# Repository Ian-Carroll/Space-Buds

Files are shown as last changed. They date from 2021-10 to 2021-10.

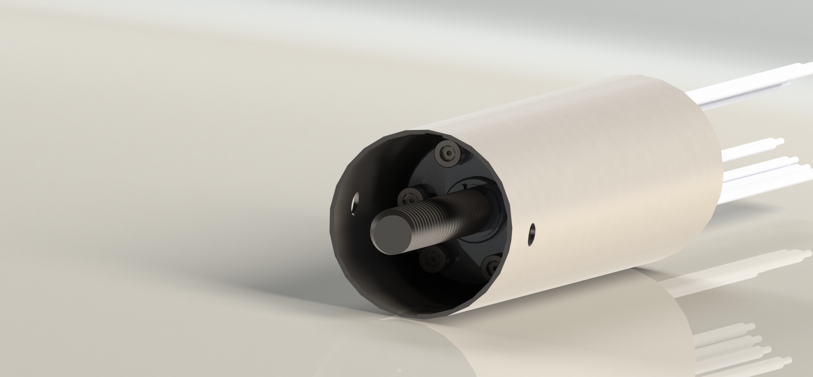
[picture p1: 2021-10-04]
Mechanical/Renders/male_side.jpeg

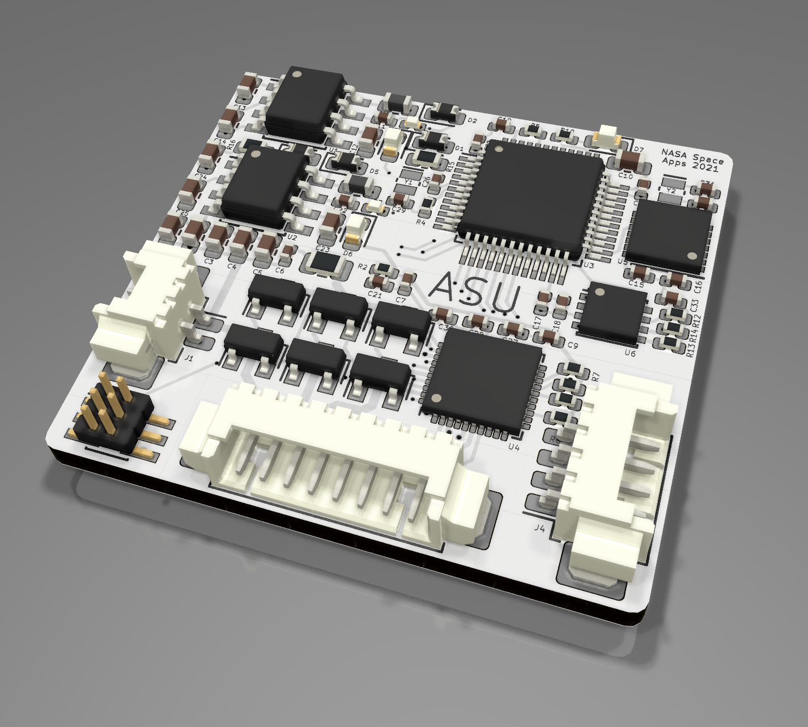
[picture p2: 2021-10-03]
Electrical/Renders/right_angle.png

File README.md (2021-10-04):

# Space Buds 

Space Buds team repository for NASA's 2021 International Space Apps Challenge - "Let It Go (Without A Bang)".

Please find our pitch video [here](https://www.youtube.com/watch?v=mZa6cD9xq2c), or feel free to browse this repository for more information. This README provides an overview of the information contained within the repository.

We would also like to highlight our design report, which can be found under `Documentation/report.pdf`.

## Mechanical Design
ezgif com-gif-maker
[Please note that the gearbox casing should not be spinning in the above animation, and the spring is missing]




[Please note that the spring should be compressed in the above render]

## Electrical Design

left_angle
right_angle
layout
schematic

## Documentation Files
File | Contents
---- | --------
`Documentation/report.pdf` | A complete design report detailing every aspect of our project. Includes renders, drawings and references.
`Documentation/presentation.pdf` | Our 5-slide pitch presentation, presented [here](https://www.youtube.com/watch?v=mZa6cD9xq2c).
`Documentation/Datasheets/Electrical/` | Datasheets for all off-the-shelf mechanical components used in our design.
`Documentation/Datasheets/Mechanical/` | Datasheets for all off-the-shelf electrical components used in our design.

## Mechanical Files
File | Contents
---- | --------
`Mechanical/animation.mp4` | An animation of the system deploying.
`Mechanical/Drawings/SolidWorks/` | SolidWorks mechanical drawings files.
`Mechanical/Drawings/Images/` | SolidWorks mechanical drawings as JPEG or PDF files.
`Mechanical/Models/SolidWorks/` | SolidWorks 3D model files.
`Mechanical/Renders/` | Mechanical part renders.

## Electrical Files

File | Contents
---- | --------
`Electrical/KiCad/` | KiCAD electrical CAD files for the PCB.
`Electrical/Renders/` | Renders of the PCB, generated by KiCAD.
`Electrical/layout.png` | An image of the PCB's layout.
`Electrical/schematic.png` | An image of the PCB's schematic.

## Contributors

* Noah Bailey
* Ian Carroll
* Aidan Clark
* Nick Cusack
* Madison Squires
* Shane Williams

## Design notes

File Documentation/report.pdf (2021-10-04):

October 2nd & 3rd, 2021 | All Screwed Up!

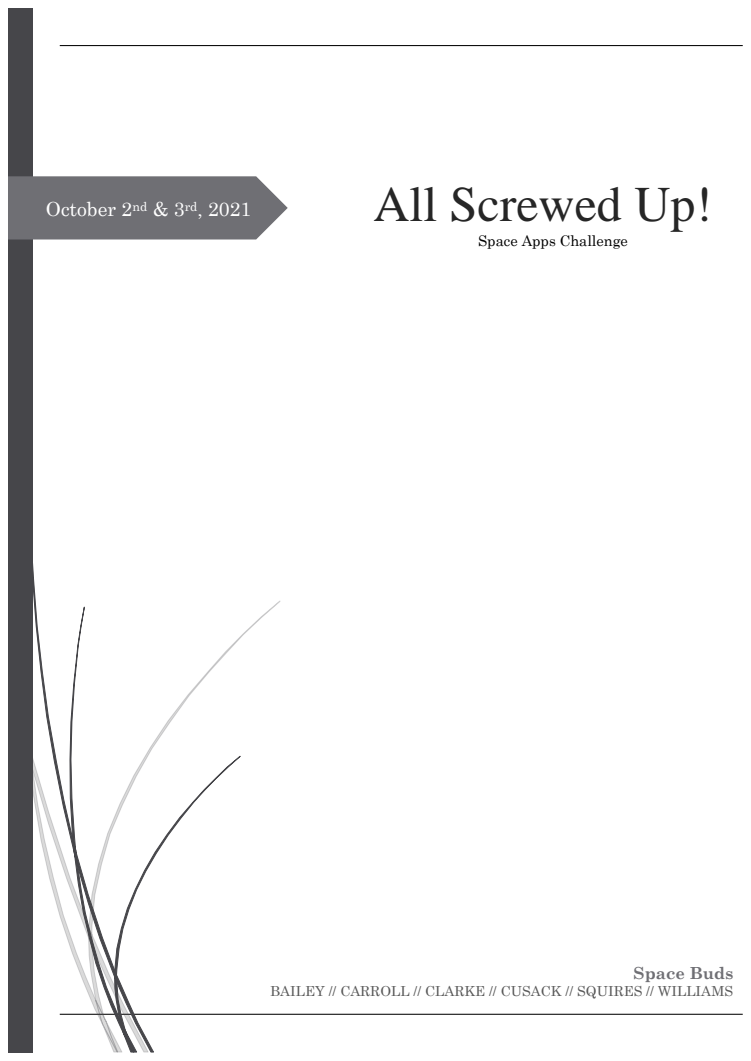
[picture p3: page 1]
Space Buds

Space Apps Challenge

BAILEY // CARROLL // CLARKE // CUSACK // SQUIRES // WILLIAMS

All Screwed Up! | Space Buds
Page | ii

## Table of Contents

Page | iii

Page | iv

## List Of Acronyms

By order of appearance

Acronym -=-=-=-=-=-=-=-=-=-=- Expansion

MUN | Memorial University of Newfoundland
ECE | Electrical Computer Engineer
CAD | Computer Automated Design
CWSF | Canada Wide Science Fair
STEM | Science, Technology, Engineering, Mathematics
NASA | National Aeronautics and Space Administration
FEA | Finite Element Analysis
3D | Three-Dimension // Three-Dimensional
PCB | Printed Circuit Board
CAN | Controller Area Network
ASU | All Screwed Up!
RPM | Revolutions Per Minute
W | Watt(s)
mm | Millimeter(s)
A // Amp | Ampere(s)
V | Volt(s)
N-m | Newton-meter(s)
N | Newton(s)
IC | Integrated Circuit

## 1 – Meet the Team

The Space Buds team is composed of six Engineering students enrolled in Memorial University

of Newfoundland. All members of the team are in their third year of the program, with an

expected graduation in 2024. The team, composed of two Mechanical Engineering students, two

Electrical Engineering students, and two Computer Engineering students – along with a wide

variety of work experience and interests – is capable of handling a large variety of challenges of

any sort.

## Noah Bailey

Coming from a family full of engineers and scientists, Noah grew up eager to study and become

an engineer just like those around him. A resident of Newfoundland his whole life, Noah is

starting his third year of Electrical Engineering at MUN. Noah developed a love for all things

computer and electrical at a young age, guiding him to inevitably study within the Electrical

Computer Engineer (ECE) program

provided at his local university.

He is interested in computing hardware,

sound engineering and music production,

physics, graphic design, and writing.

His skills include coding in various

languages, mathematics, and Computer

automated design.

Noah is competing in the Nasa SpaceApps

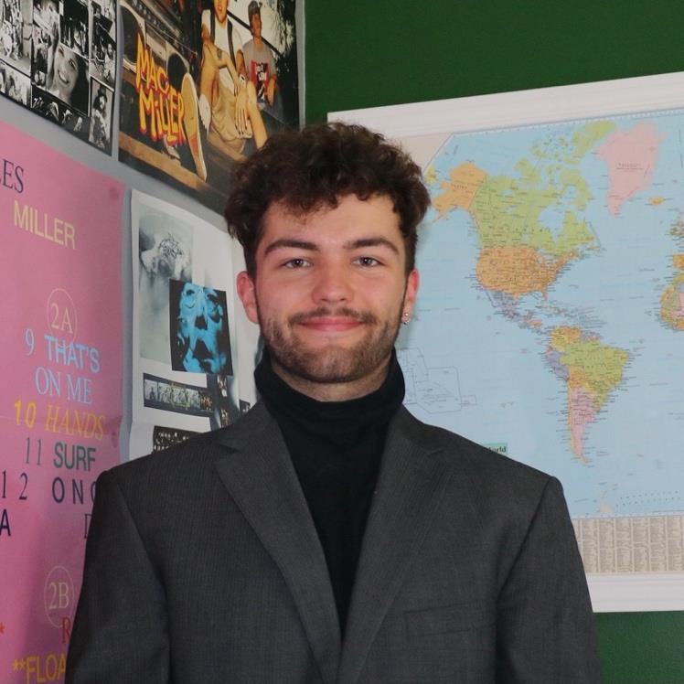
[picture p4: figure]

challenge for his first time this year and is hoping to make a big impact along with his talented

team members and classmates.

## Ian Carroll

Ian is starting his third year of Computer Engineering at Memorial University. He is always

eager to learn something new; over the last year, Ian

has learned numerous programming languages and

frameworks, taking a particular interest in

electronics and embedded system development.

Ian’s interests include choral singing, performing in

plays and musicals, and playing basketball. This

year is the first time Ian has competed in the Space

Apps international hackathon. However, he is very

excited to learn new things about hardware

development and apply them to real-world problems.

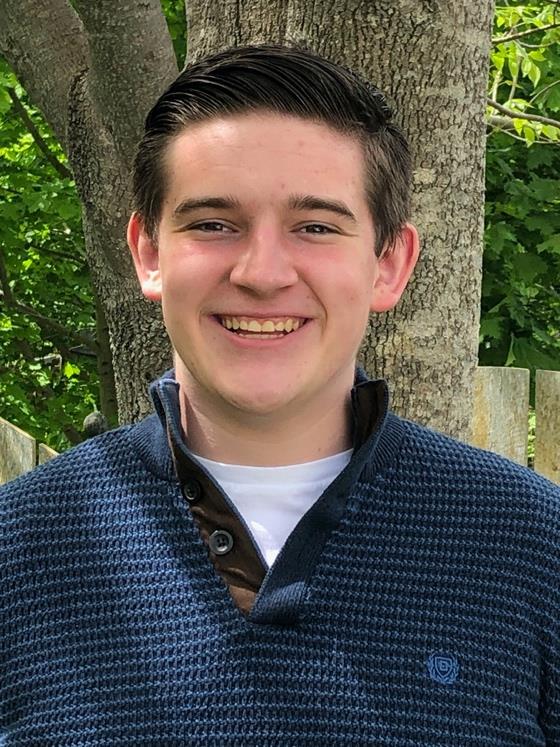
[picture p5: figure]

Ian's already existing skills include C/C++ development for embedded systems, C#

programming for cross-platform applications, and various applications of CAD development.

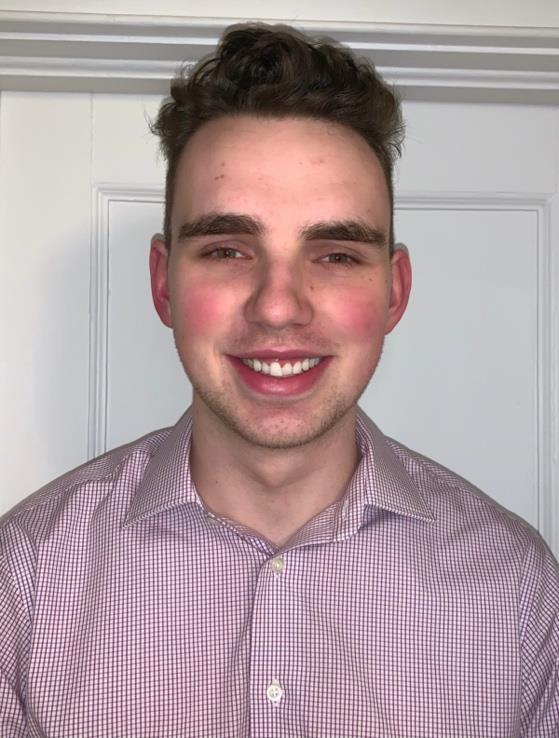
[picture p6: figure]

## Aidan Clark

Aidan Clark is a third-year Mechanical Engineering

student from a small town in Nova Scotia, currently

studying at Memorial University of Newfoundland.

Growing up, Aidan always had an interest in

learning more about how things worked - which is

why he decided to pursue a degree in engineering.

In his free time, he enjoys spending time outdoors,

exploring the rugged Newfoundland coast, or playing

volleyball.

This is Aidan’s first Space Apps competition; however, he is excited to have the opportunity to

further refine his engineering skills. Aidan’s pre-existing skills include project management,

computer-aided design, finite element analysis, Python, and public speaking.

## Nick Cusack

Nick Cusack is a third year Electrical Engineering

student at Memorial University of Newfoundland.

Growing up in Saint John, New Brunswick, Nick

enjoyed racing bikes, park skiing, and snowmobiling.

From the age of eight years old he decided he wanted to

become an Astronaut which is why he decided to

participate in this challenge.

He’s always had an engineer’s mindset which can be

seen from his bronze medal at the Canada Wide

Science Fair (CWSF) in grade eight for building a

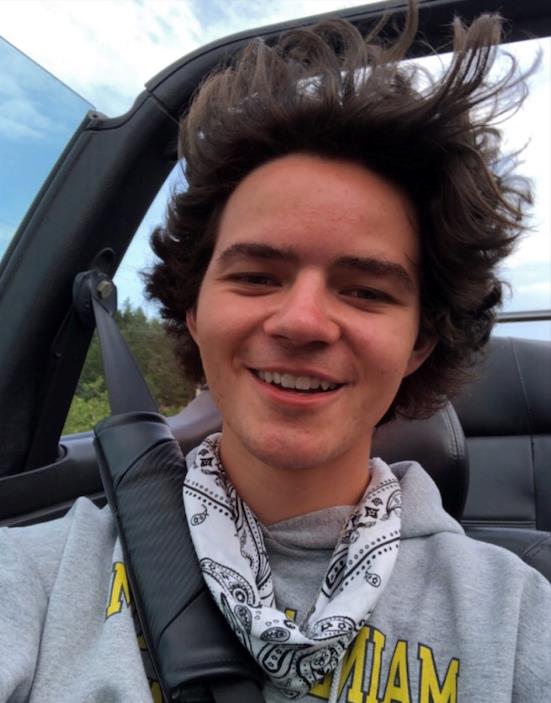
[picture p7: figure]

prosthetic arm. Or competing again in the CWSF in grade nine for building a regenerative

system for electric cars.

His latest project has been his company Cusack Innovations and their first product Folkins.

Folkins is a distracted driving detection system named after the passing of his two friends the

year Cusack Innovations was founded.

## Madison Squires

Madison is currently a third year Mechanical Engineering student at Memorial University of

Newfoundland. Madison was first exposed to Engineering in her junior high robotics team, and

ever since then she was driven to pursue a STEM (Science, Technology, Engineering,

Mathematics) career.

Madison is the President of her school’s

Engineering Society and has volunteered

countless hours for the benefit of her fellow

classmates.

Outside of school, she has many hobbies and

interests that include playing guitar, hiking

trails, and taking photographs. Madison’s work

experience ranges from oil and gas to healthcare,

so her wide variety of skills were an excellent

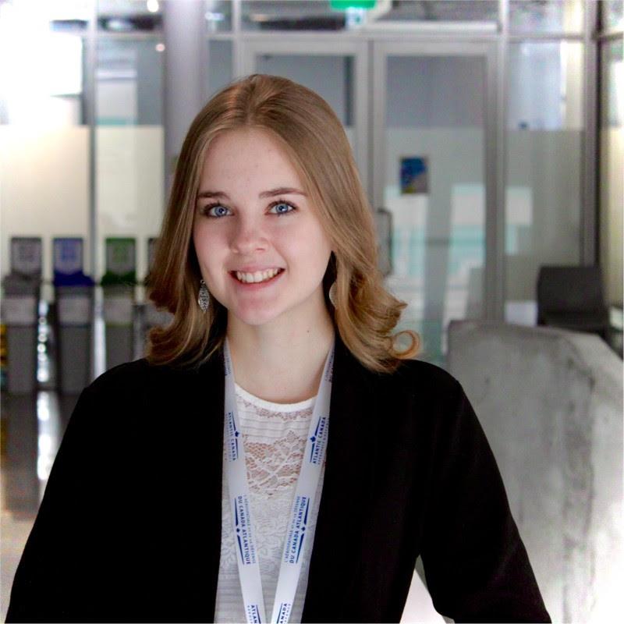
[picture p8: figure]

addition to the Space Buds team. She is thrilled to be a part of this year's NASA Space Apps

Challenge.

## Shane Williams

Shane is a third-year Computer engineering student at Memorial University of Newfoundland.

Shane’s exposure to engineering started in high school, when he competed internationally with

an underwater robotics team and interned at a local tech company.

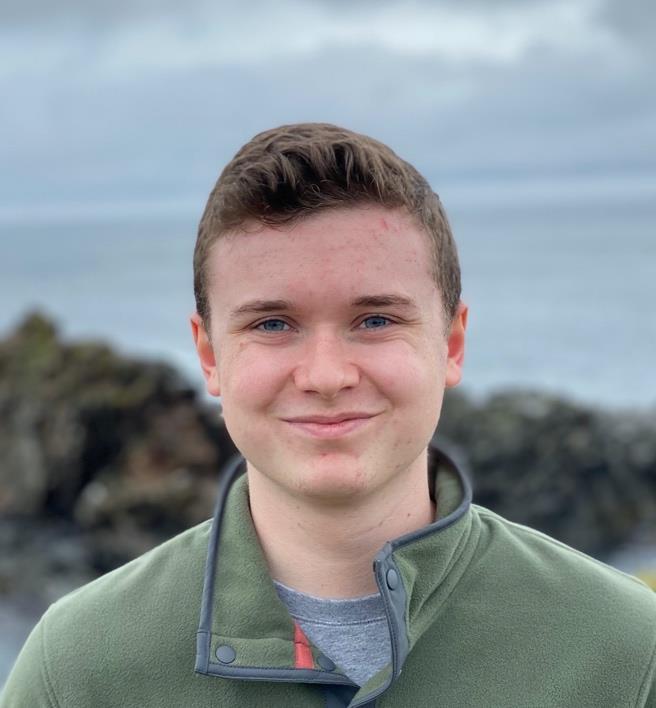
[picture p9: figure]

Shane has since worked in the space industry

with Toronto’s Kepler Communications, where he

wrote ground station software and nanosatellite

firmware. He currently works at NVIDIA where

he is creating internal development PCBs and

software for NVIDIA graphics developers.

Shane is also a member of Memorial University’s

Killick-1 Cubesat team, where he writes ground

station software.

Shane’s skills include PCB design and embedded software development, and he looks forward to

applying these digital design skills to this year’s Space Apps challenge.

## 2 – The Challenge

The purpose of this project was to compete in the tenth annual NASA-hosted Space Apps

challenge, which took place on the second and third of October 2021. Within Space Apps, there

are hundreds of thousands of students competing in various challenges, and the Challenge that

was selected by the Space Buds team was “Let It Go (Without a Bang)”.

## What is Space Apps?

NASA's International Space Apps Challenge is a hackathon over two days that has engaged

over 150,000 student programmers and engineers in over 150+ countries in previous years. This

competition utilizes NASA's open-source data to allow participants to solve real-world problems

and challenge their minds through technological developments, whether mobile application

development, videogames, or hardware design. This year, there are over 25 challenges to choose

from for each team formed with a maximum of six members. Additionally, to mark the 10th

annual Space Apps Challenge, NASA has partnered with nine international space agencies,

keeping the largest annual global hackathon ever-growing!

## Let It Go – Without a Bang

As seen in the challenge’s description, letting things go in Space is often a high-shock event. The

Let It Go (Without a Bang) Challenge tasked the participants to design a device that can cut a

parachute reefing line, a cable, or a bolt for an adapter ring, or instead, to design a mechanical

separation device that can release two parts from one-another in space without the use of

pyrotechnics – a commonly used technique in most current-day equipment.

Spacecraft require many different release devices for various components within the craft. Some

examples are detaching from a rocket, releasing parachutes for landings, and enabling

deployables to expand into space. As mentioned above, the current most common approach is to

make use of pyrotechnics, however this is something that will ideally be moved away from in

the near future and replaced with more eco-friendly and reusable options – once it goes boom, it

can’t go boom again! Pyrotechnic tools require extra safety precautions, as the large impact load

– or shock – of the actuation of the device can be upwards of tens of Gs.

## Design Constraints

The challenge was provided with numerous specifications and design objectives that must be

met. For example, it is essential that the device should survive temperatures ranging from as

cold as -50°C, and up to as hot as 80°C. It should be able to operate within a smaller range, of

0°C to 40°C. It is mentioned that heaters are permitted.

No debris should be released into space. All components must remain attached or must be

captured by some mechanism so that they are not permitted to fly free. We do not want to

create any more space junk!

The size constraints of the design are pretty tight. When working with Spacecraft, size is very

important and thus having strict tolerances for components and mechanisms is essential. The

device is required to be smaller than a cylinder with a length of fifteen centimeters and a

diameter of two centimeters. It must weigh less than one kilogram in total.

The device requires a high reliability factor in order to be a viable option for use on a Spacecraft.

Thus, it is said that the device should actuate without error upwards of 99.5% of the time. Also,

the device has access to 20 watts (W) of power but may not draw more.

## 3 – The Idea

The Space Buds team devoted the first portion of time during the Hackathon to coming up with

a viable idea for the design. Operating under the constraints of the challenge and attempting to

make the most resourceful and useful design they could, the team began by considering all of

their options and ideas for the challenge. The group discussion eventually led to a decision, and

an action plan. The team divided the work to be done and began to bring their design to life.

## Initial discussion

At the start of the day, the team began brainstorming different ways to cut a parachute reefing

line without pyrotechnics. This thought transitioned into cutting a rope using a linear actuator,

then using pneumatics, and lastly, using hydraulics. Given the conditions of outer space, all of

these designs were deemed unusable and would provide an unsatisfiable solution to the

problem.

After this discussion, the team decided to give a solution to separating two spaceship

components in zero-gravity. The previously stated methods were considered, although the group

agreed on using a servo motor at the core of the design.

Essentially, the spacecraft portions that need to be detached would be bounded by a cylindrical

casing protruding from each object. These encasings would engage in a handshake, where one

encasing fit just over the lip of the other. When the cylinders are locked in a handshake, they

would be locked internally via a screw, which would be detached via a servo motor rotating the

screw away from one component and allowing for the spring to propel the objects away upon

reaching the end of the threads.

## The Objectives

Two main sub-sections needed to be considered for the team to create a functional device with

the design mentioned above.

Firstly, there was the three-dimensional (3D) modelling of the entire device using SolidWorks

software. SolidWorks is a CAD – Computer Automated Design – software which allowed the

team to visualize the design, and perform a finite element analysis test, or simply a FEA test.

The plan included creating a 3D model detailing the gearbox and motor attached, the motor

mount attaching to the threaded rod, cylindrical encasing, and the threaded rod mounted to the

shaft of the second object.

Secondly, there was the modelling of all circuitries aboard the device using KiCad. KiCad is a

software similar to SolidWorks, although it is used for creating and rendering printed circuit

boards, or PCBs. The KiCad model detailed the microcontroller providing logic to the device, the

Motor Driver and Controller, the power regulator, and the CAN (Controller Area Network)

communication bus.

## Our plan of attack

Given the variety of disciplines that composed Space Buds, the team could naturally adapt to

the required work for the design. The group's vast and diverse skill set allowed the Mechanical

Engineering students to design and implement the physical 3D modelling of the device via

SolidWorks, and the ECE members of the team to design and implement the hardware needed

for the device. Throughout the two-day hackathon, Space Buds could prioritize, and complete,

necessary tasks assigned appropriately across different skillsets on the team.

## 4 – The Design

The following section of the report will discuss in detail the design that was drafted and

implemented throughout the two-day hackathon by the team. The specifications of the design,

how it functions, and some of the challenges that were faced while implementing the design,

will be explored in depth.

## The Design – All Screwed Up!

The design that we decided to implement – dubbed the “All Screwed Up!” design – is an

encasing device that can attach to entities together with enough strength for launch and travel

but is also capable of releasing the two from one another without the use of any pyrotechnics.

The design, hereafter referred to as ASU, is composed of two outer shell encasing shrouds,

which house the connecting components on both sides – that being the main entity and the

entity that we wish to detach.

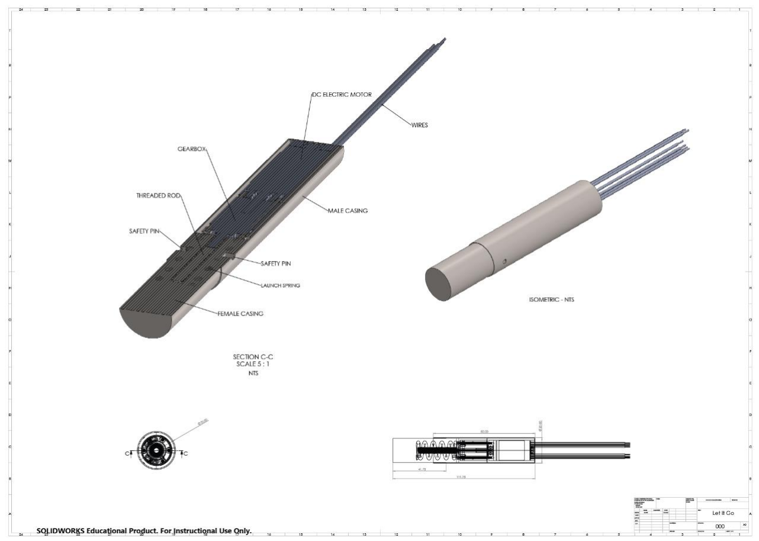
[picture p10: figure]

FIGURE 1 - THE DESIGN, ISOMETRIC VIEW

For the design of the ASU, we have realized a system that is reusable and releases no debris.

The male component – a motor with a gearhead attached to a threaded rod, encased in Shroud

A, will screw into the female end – a threaded hole encased in Shroud B.

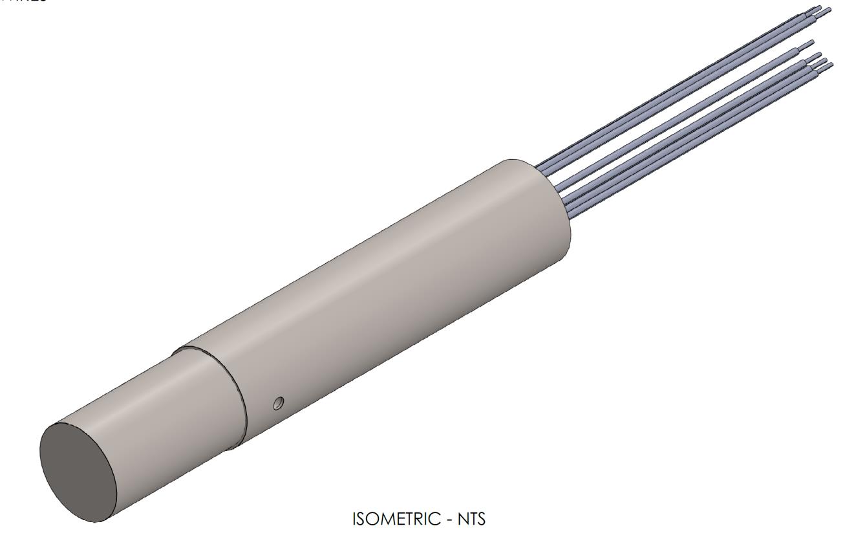
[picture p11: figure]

FIGURE 2 - THE ASU DEVICE

Another noteworthy feature of ASU is the spring. The spring will be compressed while the two

entities are attached, and as the threaded bolt is unscrewed, the spring will decompress and

force the two objects apart.

To control the motor for turning the screw head, we have designed our own printed circuit

board, or PCB, which has been specifically designed to control the ASU device.

Additionally, the system is easily reusable, as the motor can operate both ways, meaning it is

possible to attach to objects together – compressing the spring and screwing the bolt into the

socket – as well as detach two objects – decompressing the spring as the threads are unwound.

The male thread of the ASU device may also be used for attaching to numerous different female

entities, so long as the entity that we wish to attach has the appropriate female portion of the

ASU mounted to it.

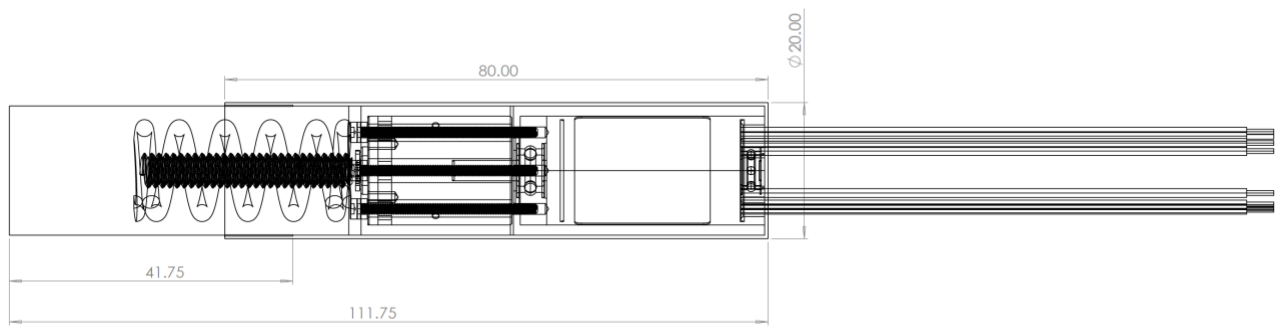
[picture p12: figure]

FIGURE 3 - ALTERNATE ASSEMBLY VIEW

## How it Works

A custom designed PCB operates a motor. The motor travels through a gearhead, lowering the

revolutions per min – RPM – and increasing the torque. The slow-spinning, high-torque shaft is

friction-welded to a 10-24 threaded titanium alloy rod. Note - all titanium alloy used is Ti-6AI-

4V Titanium alloy. When combined, the two encasings hold these elements, as well as a

compressed spring, in place. The threaded rod screws into a port, holding the two entities

together. As the motor activates and begins unscrewing the rod, the spring decompresses. Once

the threads are fully separated, the spring fully decompresses, forcing the two entities apart.

## Challenges Faced

Vacuum Compatibility

ASU was designed to be fully vacuum compatible. There are no airtight compartments to

prevent pressurization as the part enters space.

Electrical components were also chosen with vacuum compatibility in mind. Electrolytic

capacitors were avoided as they can become pressurized in space, and banks of parallel ceramic

capacitors were used instead.

Thermal Design

All components chosen are rated for storage at the extreme temperatures of space, and are also

rated to operate from 0 °C to 40 °C, as specified.

The casing, motor and gearbox also have a significant amount of mass and therefore thermal

capacity, which can help cool the motor during operation. Overheating isn’t of significant

concern as the motor will only be run for seconds at a time, once per mission.

Cold Welding

Cold welding is of concern when similar metals make contact in space. This can be prevented by

using materials and coatings that have been shown not to cold weld through significant flight

heritage.

Choosing an Appropriate Motor

It proved to be quite the challenge to find an appropriate motor for the design of ASU. It is quite

hard to find a small enough motor to fit the size constraints that is able to create the amount of

torque required for connecting and separating the two entities. This led to the implementation

of the gearhead, which allowed us to prioritize size and power constraints when it came to the

motor – thus we could ignore the torque as it would be handled by the gear ratios.

Choosing Materials

Choosing materials that are space-worthy is a challenge. Not all materials are strong enough or

have the properties required for space launch, or space travel. We ended up choosing to create

any of our custom-designed components out of Ti-6AI-4V Titanium alloy. This material has been

extensively researched and is frequently the material chosen for spacecraft and satellites in the

current day. All of the sourced components of ASU have been checked to ensure that they

operate within the desired temperature range and can withstand the pressures and forces they

will experience throughout their use.

Computational Requirements

In order to run simulations, create renders, run calculations, and create CAD models, we

require a massive number of computational resources. The Space Buds team, operating within a

strict time constraint, had to be very resourceful as a whole in order to collect all of the desired

data in time. This required great communication, planning, and time management as a unit.

## 5 – The Components

Each component of the ASU design has a specific and important function. Each piece

individually must be able to work well with each other as a whole to perform the desired action

safely, reliably, and consistently. When choosing the components of the ASU, every single detail

had to be considered, no matter how minute. For example, the chosen materials needed to be

resilient enough to survive launch, as well as strong enough to withstand space. They needed to

be light and fit the size constraints. Power was a constant consideration, as the design may only

consume 20W of power. Each component is accompanied by a specification drawing, detailing

the materials and dimensions.

## The Shrouds

The shrouds, or the casings, are two titanium alloy tubes that are keyed to lock within one

another. The male shroud contains the components which are required to remain on the base

module, being the motor, gearhead, spring, and threaded bolt. The female shroud protects the

entity which will be detached from the base module and released into space. Within the female

shroud is the hole in which the threaded bolt will be wound.

The shrouds protect all the components within from being damaged or destroyed throughout

launch and flight. They are made from a sturdy and reliable metal alloy. As seen in the figure

below, they are XXX millimetres (mm) long, and YYY mm wide.

The keying on the casings is an essential piece of the design. They are keyed to lock into one

another once the two entities are connected. This prevents motion in the perpendicular plane,

and also prevents rotation. Once attached, we do not want the two entities to shift side to side

or to rotate out of the initial position, thus creating a need for a male and female key on the

shrouds. With the shrouds, we are not worried about parallel motion, as this is stopped by the

threaded bolt, as will be explained within the following sections.

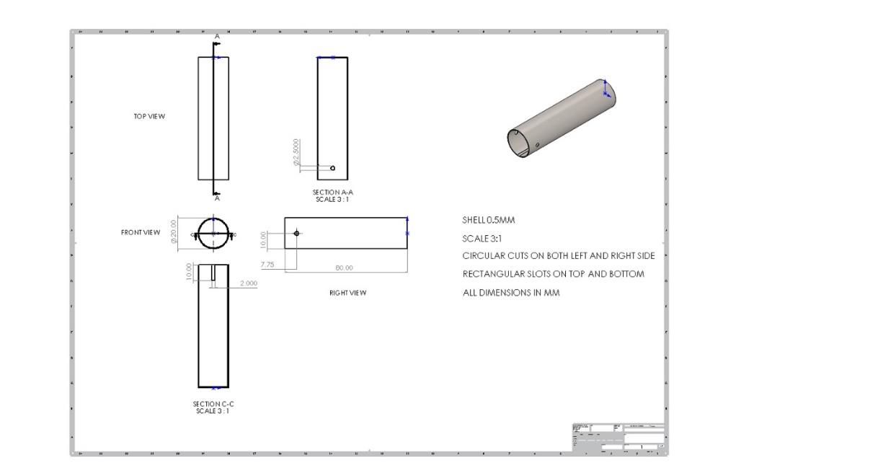
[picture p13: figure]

FIGURE 4 - THE MALE SHROUD

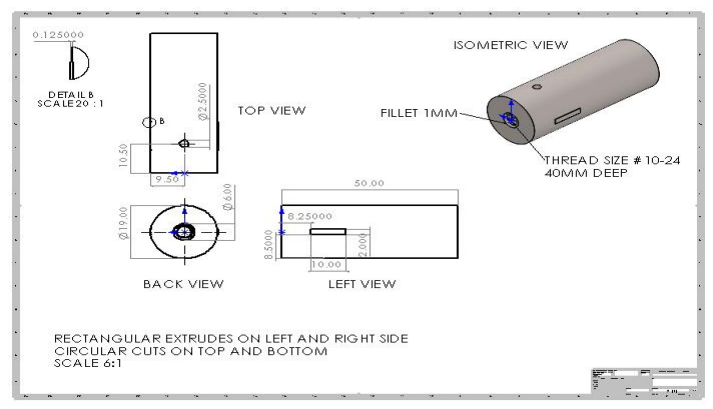
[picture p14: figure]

FIGURE 5 - THE FEMALE SHROUD

## The Spring

One of the critical components required for the push-off during the detachment phase is the

spring. This component is made from INSERT MAT, and it is X mm by Y mm by Z mm by

WIDTH mm in size. The compressed spring was selected to perform optimally for the needs of

the design. It does not cause any abrupt movements, smoothly letting the female shroud push

off the male shroud with a small force – as not much force is required in zero gravity.

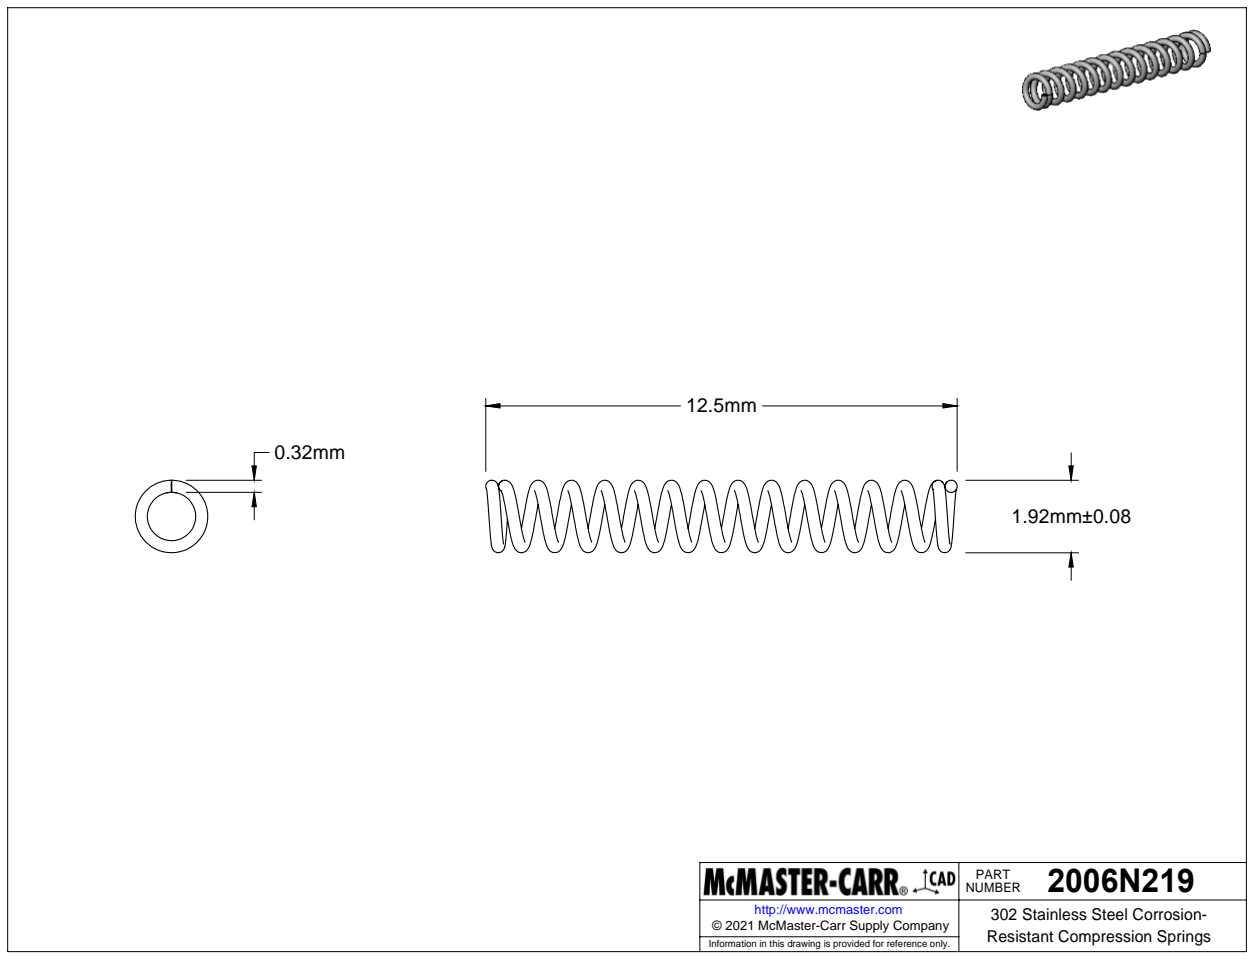
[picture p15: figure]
PART 2006N219 NUMBER

FIGURE 6 - THE SPRING

Choosing the spring was an interesting process, as the team required a spring with a specific

spring coefficient. These are based on length, thickness, material, and diameter, as well as

number of turns. All of these characteristics needed to be considered when choosing and

designing the spring.

## The Motor

Choosing an appropriate motor for the design proved to be one of the most challenging tasks of

the entire design process. The motor used within the ASU is a brushless direct current (DC)

motor. The motor selected by the space bud team is a Portescap motor, namely the 16ECP36 8B

380 .01 Ultra EC Slotless Brushless DC Motor.

http://www.mcmaster.com © 2021 McMaster-Carr Supply Company | 302 Stainless Steel Corrosion-Resistant Compression Springs

Information in this drawing is provided for reference only.

This motor weighs 41 grams, and measures only 16mm in diameter, at 36mm in length with a

shaft of 10mm. It is important to note that the 10mm shaft will be attached to the gearhead.

With a maximum continuous current of 0.3 amperes, or amps (A), operating at a voltage of 24

volts (V), the maximum power draw of the motor is 7.2W.

The motor sports a maximum RPM of 63,000, but this is much higher than the team required

and will not be used. In fact, the gearhead attached to the motor will lower the revolutions per

minute significantly and increase the torque.

The motor can function within a high temperature range, from -30°C to 100°C. It uses an odd

wiring scheme, which was taken into account when creating our PCB, as will be seen in a later

section.

The motor’s data sheet and specification data can be seen in the following figures.

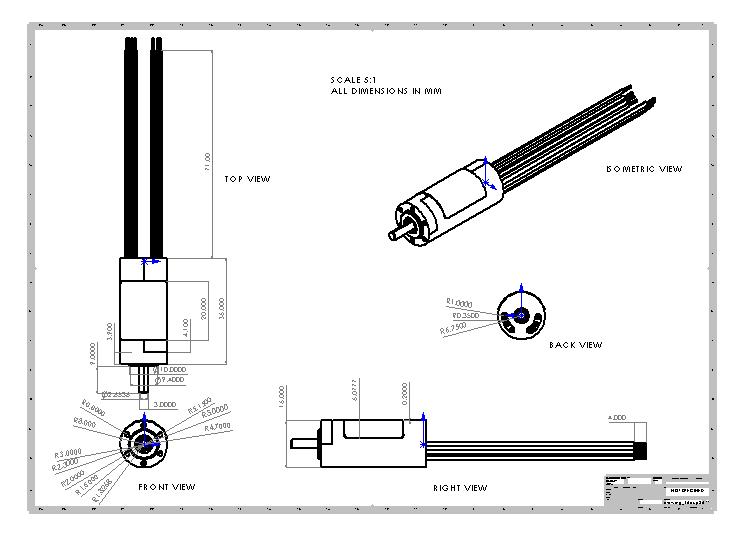
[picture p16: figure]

FIGURE 7 - R16ECP36 MOTOR

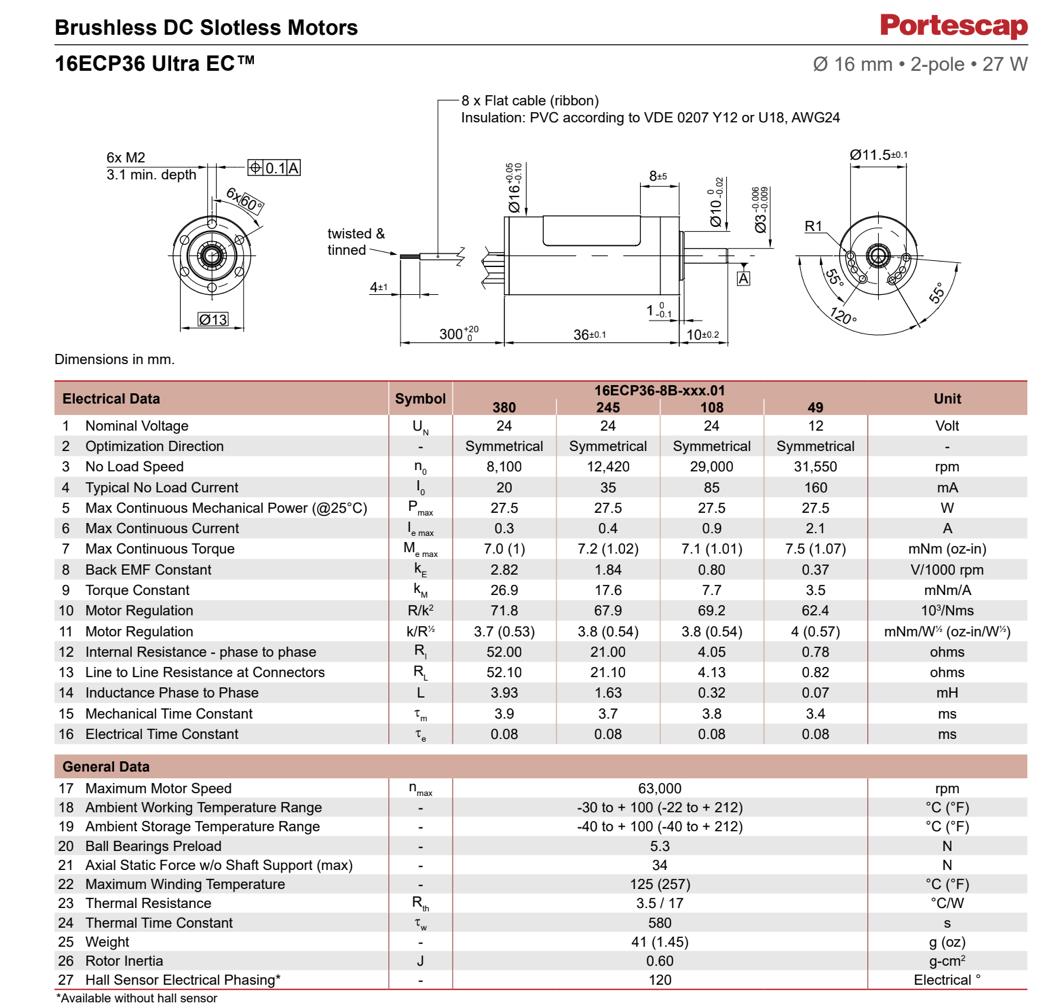
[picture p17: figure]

FIGURE 8 - MOTOR DATA SHEET

## The Gearhead

The part responsible for providing enough torque to rotate and push the screw away is the

gearhead. Given the previously mentioned specifications of the brushless DC motor, the

gearhead was able to attach to the head of the motor with a conversion ratio of 915, allowing for

a significant increase of torque ability.

The chosen gearhead is a Portescap gearhead specifically designed to pair with the chosen

Portescap motor, the R16-0-915 Sleeve Bearing Mini Motor Gearhead. It can operate within a

temperature range of -30°C to 85°C, which is ideal for the ASU application. It weighs only 19

grams, and is highly efficient, with four gear stages, and a static torque of one Newton-meter

(N-m).

Lastly, two notable details of the gearhead: firstly, the size of the gearhead is 28.3 mm long by

16 mm diameter, which fits inside the constraints of the cylindrical shrouds, and secondly, it

can rotate in either direction – a key feature to ensure the reusability of the ASU device.

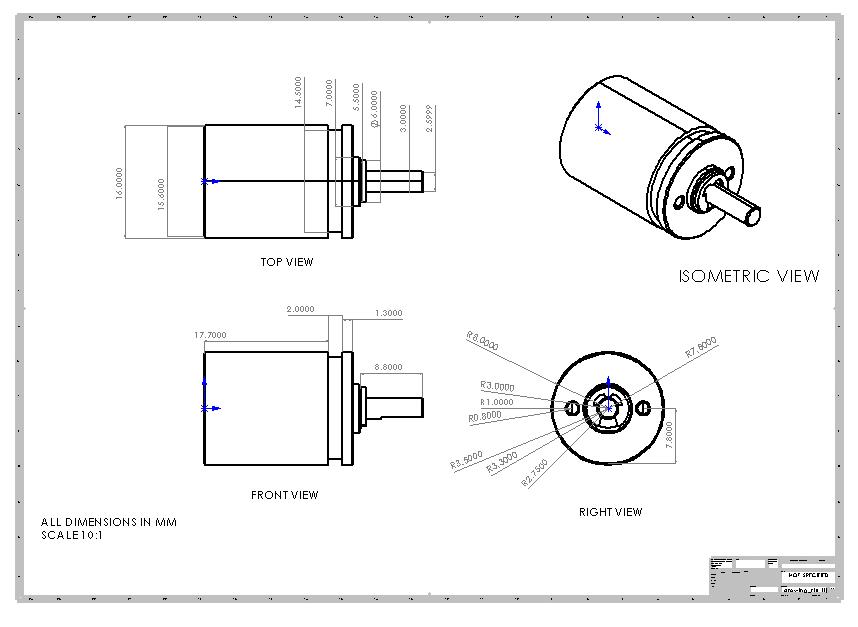
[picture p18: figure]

FIGURE 9 - R16 SLEEVE BEARING GEARHEAD

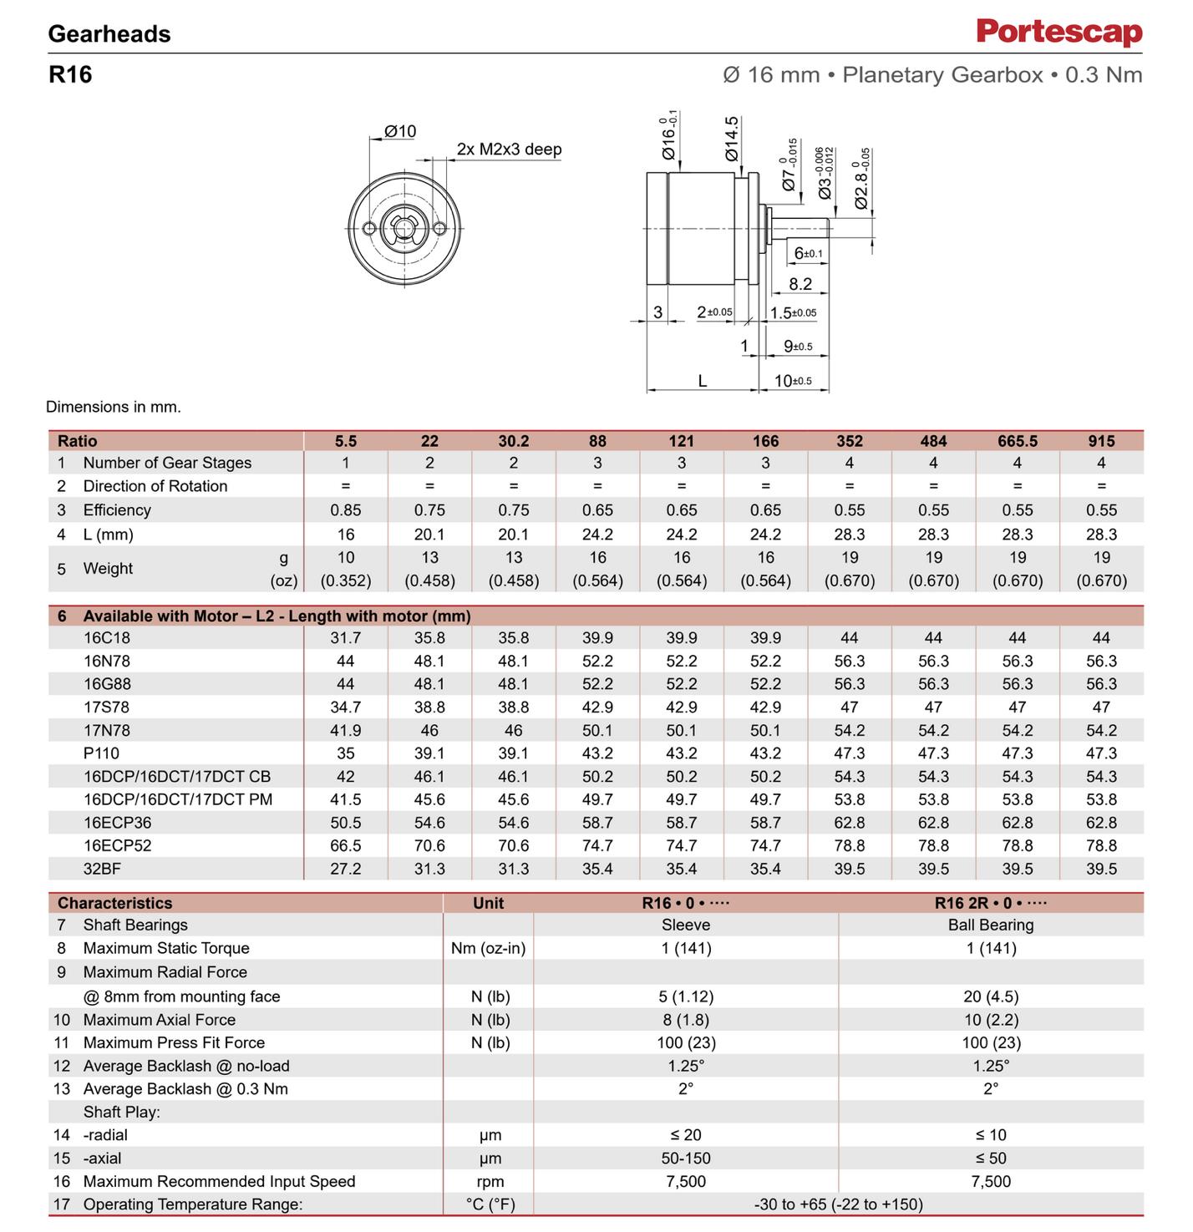
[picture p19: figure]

FIGURE 10 - GEARHEAD DATA SHEET

## The Threaded Bolt

The threaded bolt is mounted to the drive shaft of the gearhead via friction welding, a process

which is able to weld one object inside of another. The threaded bolt is bored out wide enough to

insert the shaft from the gearhead, which is when the two undergo friction welding to secure them together indefinitely. This process was decided upon as it is much stronger and more

reliable than any other method of attaching the two, such as a pin mechanism.

The threaded bolt is used to screw the male module into the female module. It is made out of

titanium alloy and is YYY mm long. It has 10-24 thread, perfect for the strength needed to

securely hold the two entities together during launch and travel. The manual pins of the ASU

travel on either side of the threaded bolt.

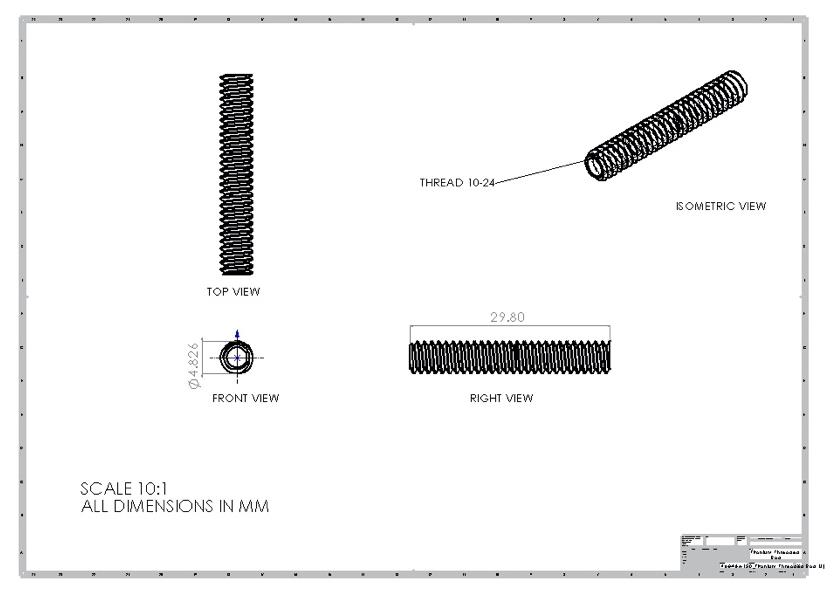
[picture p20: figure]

FIGURE 11 - THREADED ROD

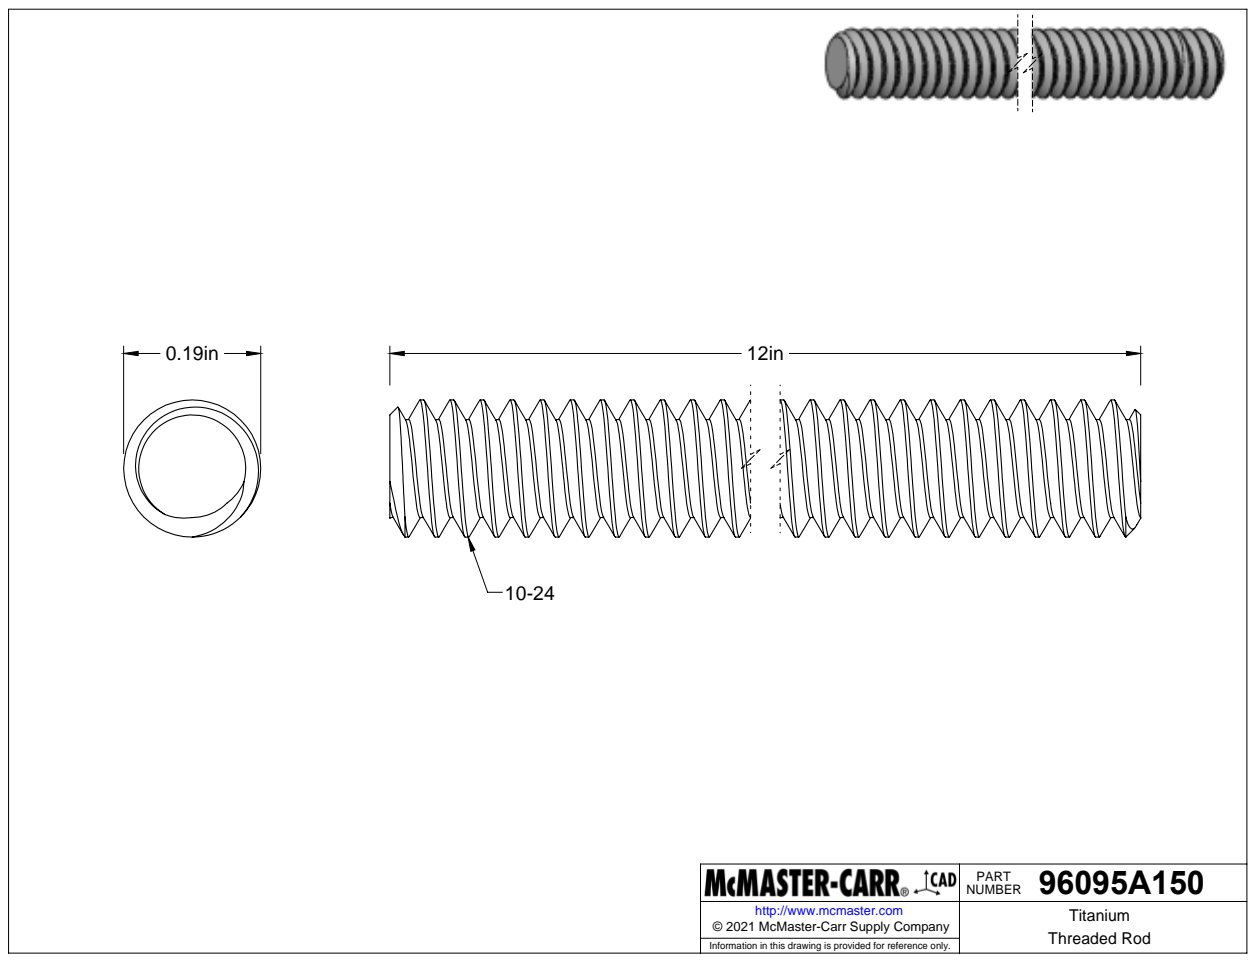
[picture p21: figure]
PART 96095A150 NUMBER

FIGURE 12 - THREADED ROD ALTERNATE DRAWING

http://www.mcmaster.com | Threaded Rod © 2021 McMaster-Carr Supply Company Titanium

Information in this drawing is provided for reference only.

## The Manual Release Pins

The manual release pins were implemented into the design of the device as a safety precaution.

When the safety pins are left in before launch, it ensures that the device will not release before

intended but must be removed before the device is launched into space.

The safety pins that we designed are X mm by Y mm by Z mm and are made of titanium alloy

metal.

The manual safety pins are simply an extra precaution to ensure the device does not

accidentally fire before it is wanted. Typical manual safety pins in modern technology are

labelled with a large tag that say “Remove Before Flight” on a large red ribbon. This is a feature

that may be implemented onto the manual pins of the ASU.

## The Printed Circuit Board

For the ASU design, the Space Buds team took it upon themselves to fully design a custom PCB

in order to drive and control the motor, which is the center piece of the design. If the motor were

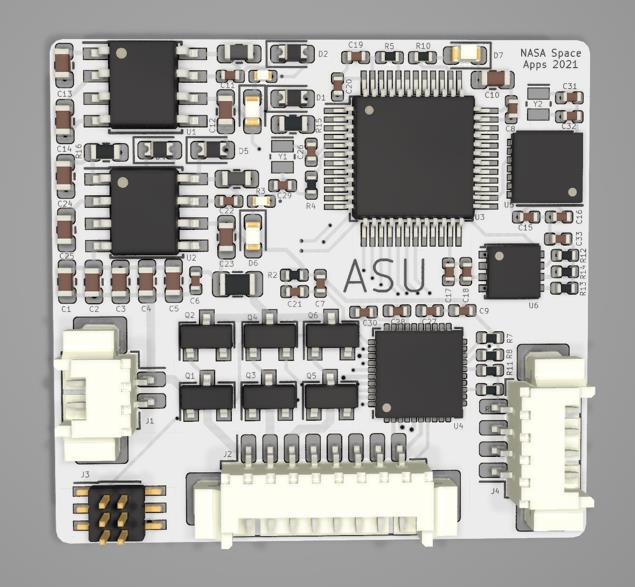
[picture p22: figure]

the heart of the design, the PCB would be the

brain.

The board designed featured numerous

Integrated Circuit elements, or IC elements.

These chips will be described in detail within the

following subsections, as well as how they all

interact with one another to achieve the desired

result.

This PCB features a low-power

microcontroller, a CAN subsystem for communication to a central controller, two power

FIGURE 13 - PCB FRONT VIEW regulators for creating 3.3 V and 5 V digital power rails and a motor controller/driver with

driver transistors.

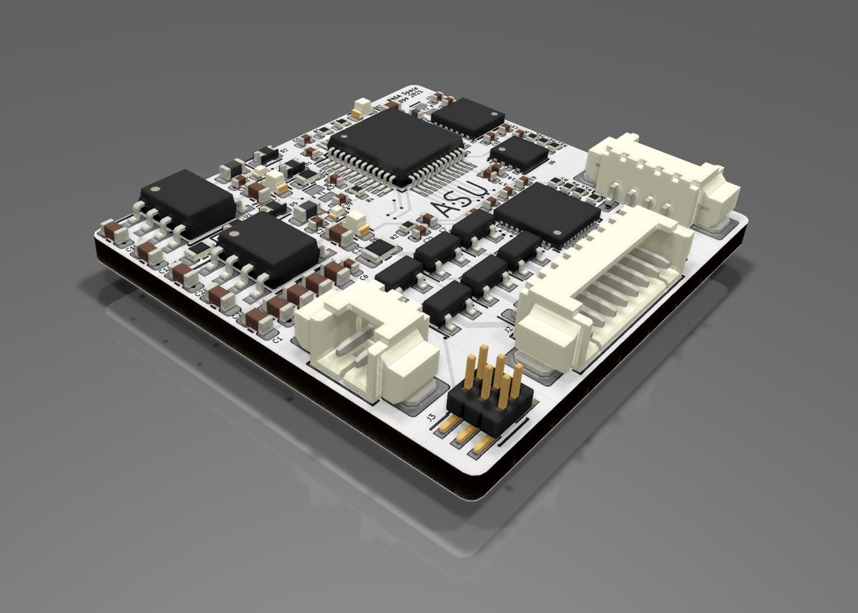
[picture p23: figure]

FIGURE 14 - PCB ANGULAR VIEW

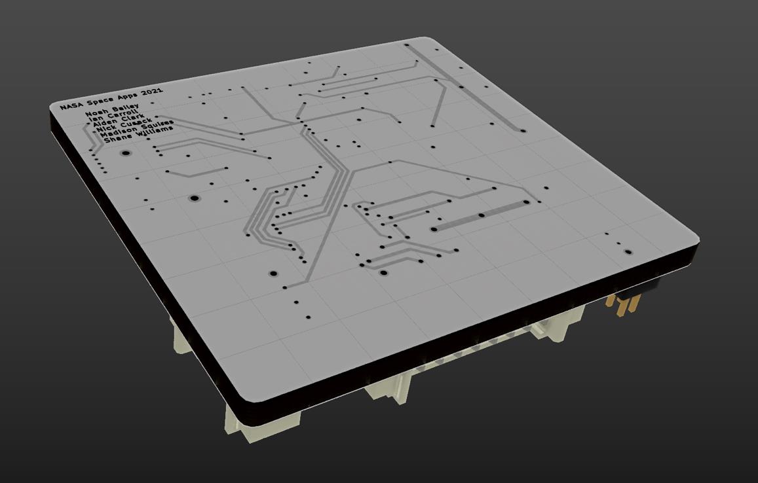
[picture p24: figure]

FIGURE 15 - PCB BACK VIEW

Microcontroller

The microcontroller interfaces with both the CAN controller and the motor driver. This allows

for CAN control of the device, as well as fault management.

The chosen microcontroller was an STM32L031C6. This microcontroller was chosen because it

met our requirements for number of pins, processor speed and peripherals, namely SPI and

PWM. Other benefits of this chip include its low power consumption, integrated temperature

sensor and significant software support.

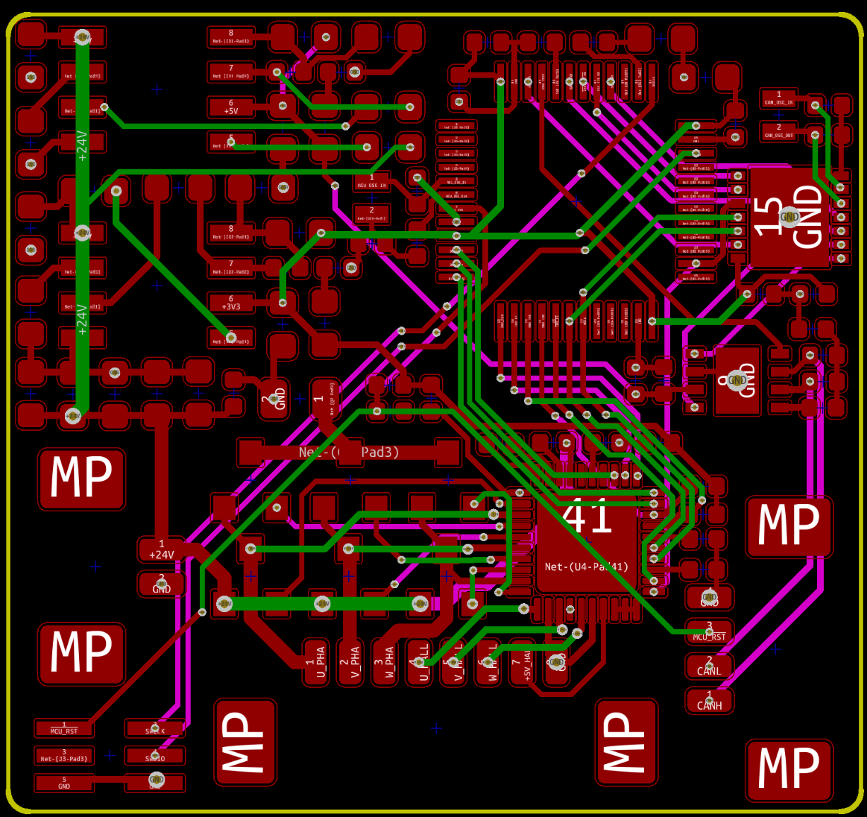
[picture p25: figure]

FIGURE 16 - PCB LAYOUT

Motor Driver / Controller

A Texas Instruments DRV8308 brushless DC motor controller/driver IC was used to control the

motor. This IC uses a closed-loop control technique which relies on the motor’s integrated hall

sensors and drives 6 Metal Oxide Semiconductor Field Effect Transistors (MOSFET).

We chose this driver because of its SPI connectivity, PWM control and because it met our

voltage and power requirements.

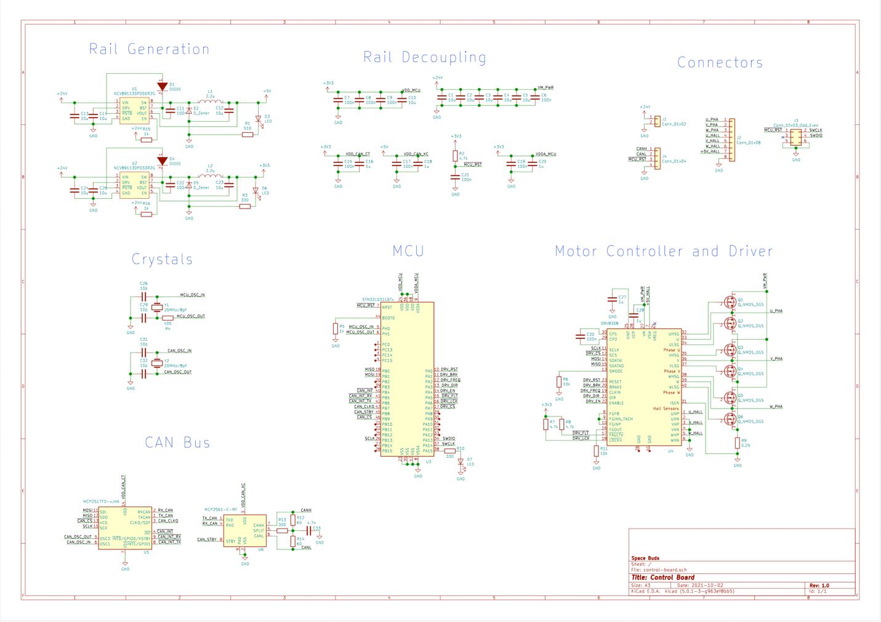
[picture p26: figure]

FIGURE 17 - PCB SCHEMATIC DESIGN

Power Regulator

We used 2 hybrid low-dropout/switching regulators to convert the 24 VDC input into 3.3 VDC

and 5 VDC rails for digital devices on the PCB, namely the microcontroller, CAN controller and

CAN transceiver. The NCV891130 power regulator was used.

CAN Bus

A MCP2517FD SPI CAN controller was used in combination with a MCP2561-2 CAN

transceiver to enable CAN control of the motor.

## Reliability & Safety

To ensure that the device is reliable, various tests were run in order to validify the 3D model

and hardware of the design. These simulations were the first step in testing the design, before a

prototype could be created and tested in real life.

One test to confirm the validity of the 3D model was using Finite Element Analysis (FEA),

where the analysis ensured that the device could withstand 4000 newtons (N) as specified in the

challenge details. This test was handled by the mechanical team and produced some interesting

results. It allowed the team to test the design quickly in a simulation environment, and to make

any necessary changes based off of obstacles encountered throughout the scientific process.

Secondly, design rule checking was used in KiCad software to verify that the PCB maintained

all connections. The design rule checking simulations were handled by the ECE team, and the

circuit board was tested in depth and any optimizations were made as seen fit.

The next step to testing reliability of the device would be to fabricate actual prototypes and see

how they function under different situations. By adjusting control and independent variables,

more specific and before unseen optimizations can be made. This may include modifying the

physical design, the PCB design, or the code used to run the electrical elements of the ASU.

When it comes to engineering of any sort, it is always of paramount importance to consider

safety. A safe design is extremely important, as a design that is dangerous not only reflects

poorly on the team that created it, but often puts others in dangerous situations.

The Space Buds makes no exceptions – safety is the number one priority. While designing the

ASU, it was always important to evaluate the risks associated with any features or components.

We asked ourselves, “Is this safe? How can it go wrong? What damage could it cause?” Followed by “How can we make this more reliable? What safety features can we implement? Is there a

better way to implement this?”

The ASU is made of reliable and well-researched materials, and has safety mechanisms in place

to ensure no assets are damaged or lost, and no people can be harmed by the device.

## 7 – Conclusion

Over the course of the tenth annual Space Apps challenge, the Space Buds team dedicated their

time and effort into designing a brand-new product, which was titled “All Screwed Up!” The

design was created to separate two entities from one another within space, after having

survived a launch.

Through hours of research and development, design, calculations, simulations, and discussion,

the team produced a design that they were happy with.

Overall, the Space Apps challenge was a fun experience for the whole team, and we look

forward to participating again in the future. The ASU design process was a remarkable learning

experience for us all, and allowed us to perfect our skills as well as learn some new skills from

each other.

The ASU design has passed all of the specifications as noted in the challenge description and

has even gone above and beyond what we thought may be possible. It is lightweight, durable,

draws little power, and is even quite scalable. The majority of components were designed and

created in-house, and the others were chosen carefully from reputable sources and companies,

who were able to provide specification data and resources to aid us in the design and

implementation.

The final design was tested under various conditions through various software simulations and

met all of our expectations and completed all of the objectives. It makes use of a slotted brushless DC motor, a gearhead, two shrouds, a threaded bolt, a spring, and a custom designed

PCB, as well as some extra safety precautions such as manual safety release pins.

The time constraint for the challenge was to complete the design within two days, which put

quite the strain on the Space Buds team, but through great communication and teamwork, the

challenge was completed.

## 8 – References

Badescu, M., Bao, X., & Bar-Cohen, Y. (n.d.). Shape memory alloy (SMA)-based launch lock.

Pasadena, CA: NASA.

Chartres, J., & Cappuccio, G. (2017, August 3). Nanosatellite Launch Adapter System (NLAS).

Retrieved from NASA: https://www.nasa.gov/centers/ames/engineering/small-sat/nlas

Garner, R. (2020, May 22). Sun-Earth. Retrieved from NASA:

https://www.nasa.gov/mission_pages/sunearth/spaceweather/index.html

McMASTER-CARR. (2021, October). 302 Stainless Steel Corrosion-Resistant Compression

Springs. Retrieved from McMASTER-CARR: https://www.mcmaster.com/2006N219

McMASTER-CARR. (2021, October). Titanium Threaded Rod. Retrieved from McMASTER-

CARR: https://www.mcmaster.com/96095A150

Microchip Technology Inc. (2014). High-Speed CAN Flexible Data Rate Transceiver. Chandler,

AZ: Microchip Technology Inc.

Microchip Technology Inc. (2017-2018). External CAN FD Controller with SPI Interface.

Chandler, AZ: Microchip Technology Inc.

NASA. (2020). Separation Device Launches New Science Payloads. Retrieved from NASA

Spinoff: https://spinoff.nasa.gov/Spinoff2020/ip_8.html

onsemi. (2018). Step-Down Regulator - Automotive, Low-Iq, Dual-Mode . Semiconductor

Components Industries, LLC.

Portescap. (2021, October). 16ECP36 Ultra EC Slotless Brushless DC Motor. Retrieved from

Portescap: https://www.portescap.com/en/products/brushless-dc-motors/16ecp36-ultra-ec-

slotless-brushless-dc-motor

Portescap. (2021, October). R16 Sleeve Bearing Mini Motor Gearhead. Retrieved from Portescap:

https://www.portescap.com/en/products/accessories/gearheads/r16-sleeve-bearing-mini-

motor-gearhead

PRODUCT DATA of 01: Aluminium and its Alloys. (n.d.). Retrieved from spacematdb:

https://www.spacematdb.com/spacemat/datasearch.php?name=01:%20Aluminium%20an

d%20its%20Alloys

PRODUCT DATA of 04: Titanium and its Alloys. (n.d.). Retrieved from spacematdb:

https://www.spacematdb.com/spacemat/datasearch.php?name=04:%20Titanium%20and

%20its%20Alloys

Reynolds, J. M. (n.d.). Materials In Space. Retrieved from NASA:

https://materialsinspace.nasa.gov/home

Sexton, A., Dayton, C., Wedland, R., & Pellicciotti, J. (n.d.). DESIGN, DEVELOPMENT AND

TESTING OF THE GMI LAUNCH LOCKS. Greenbelt, MD: NASA. Retrieved from

https://ntrs.nasa.gov/api/citations/20110016488/downloads/20110016488.pdf

STMicroelectronics. (2021, October). Ultra-low-power Arm Cortex-M0+ MCU with 32-Kbytes of

Flash memory, 32 MHz CPU . Retrieved from STMicroelectronics:

https://www.st.com/en/microcontrollers-microprocessors/stm32l031c6.html#overview

Texas Instruments Incorporated. (2021). DRV8308 Brushless DC Motor Controller. Dallas,

Texas: Texas Instruments. Retrieved from Texas Instruments:

https://www.ti.com/lit/ds/symlink/drv8308.pdf

UTIAS. (2014). University of Toronto Institute for Aerospace Studies Space flight laboratory.

Retrieved from UTIAS SFL: https://www.utias-sfl.net/

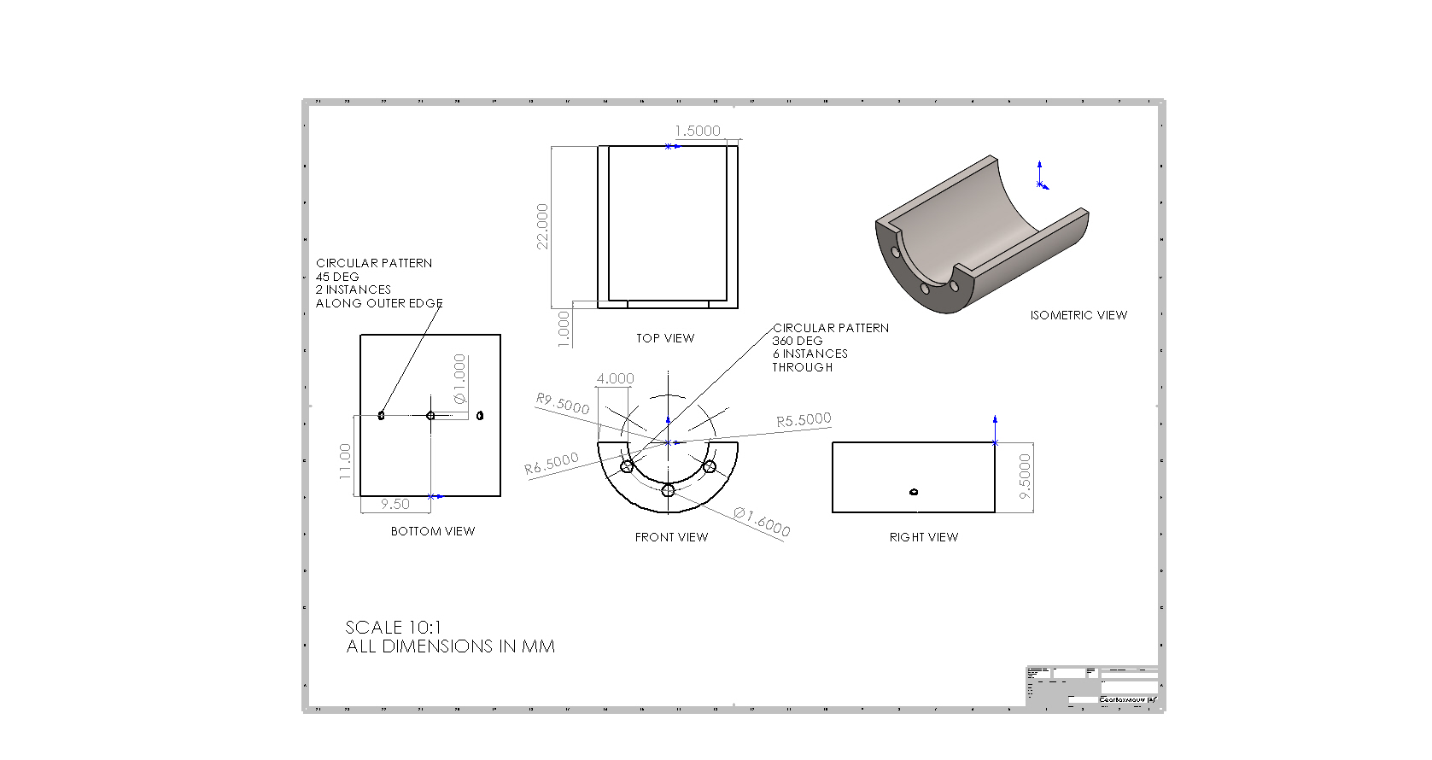
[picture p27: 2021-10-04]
Mechanical/Drawings/Images/GearBoxMount (4).JPG

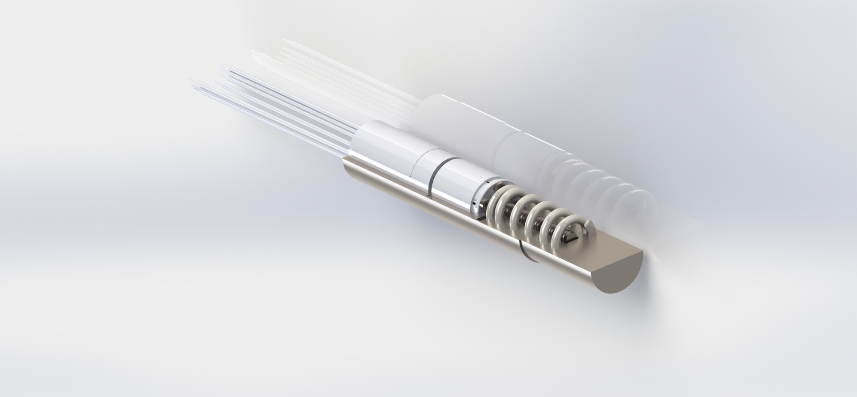
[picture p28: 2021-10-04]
Mechanical/Renders/full_system.jpeg

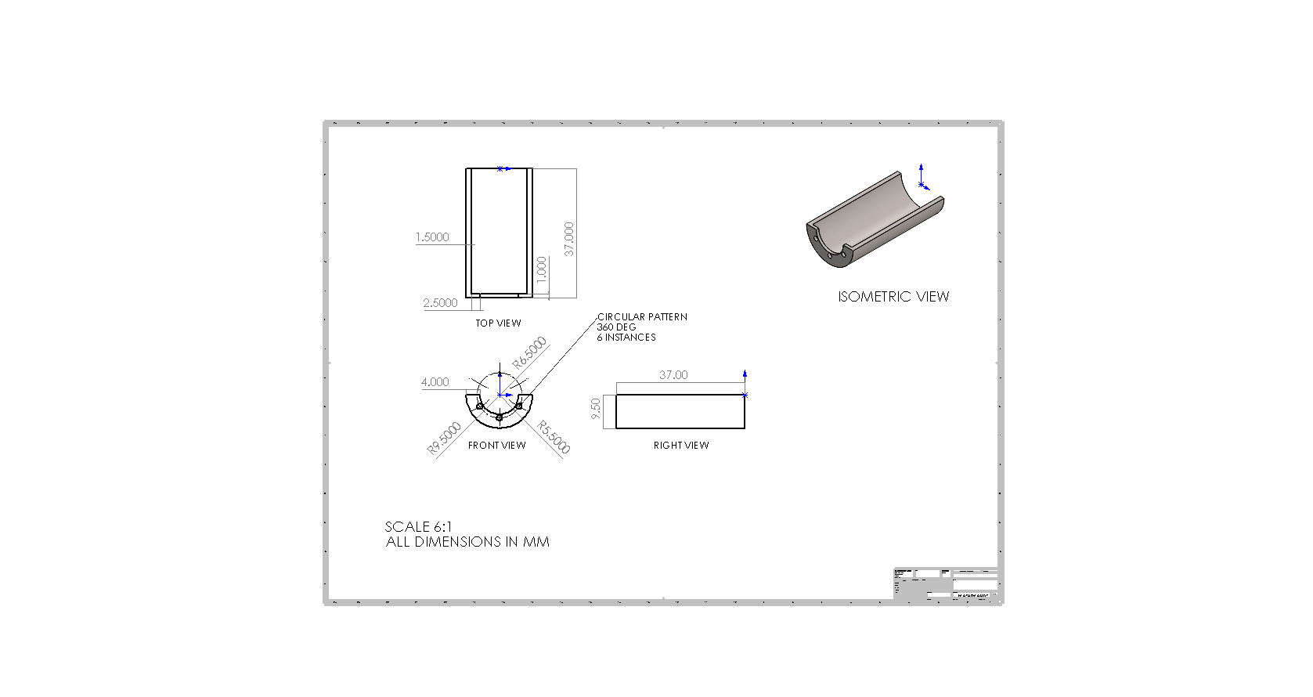
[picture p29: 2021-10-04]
Mechanical/Drawings/Images/MotorMount.JPG

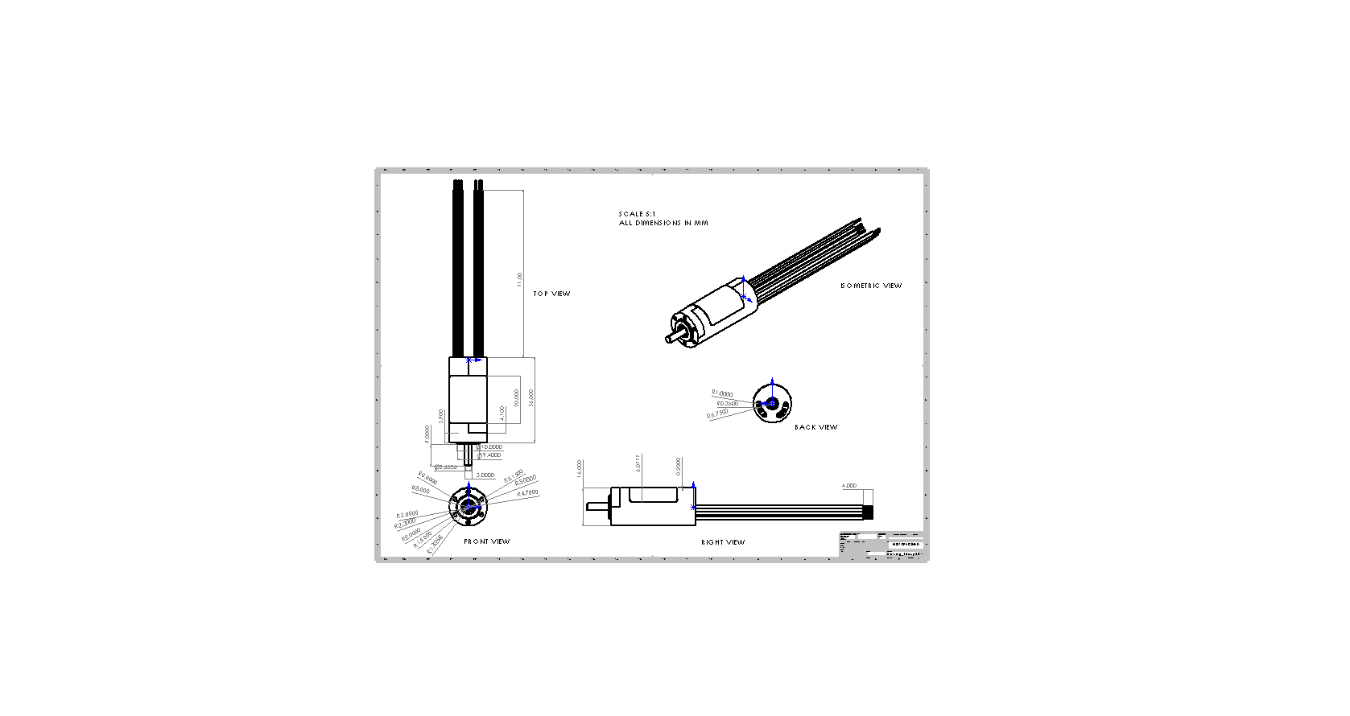
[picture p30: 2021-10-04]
Mechanical/Drawings/Images/drawing_16ecp36.JPG

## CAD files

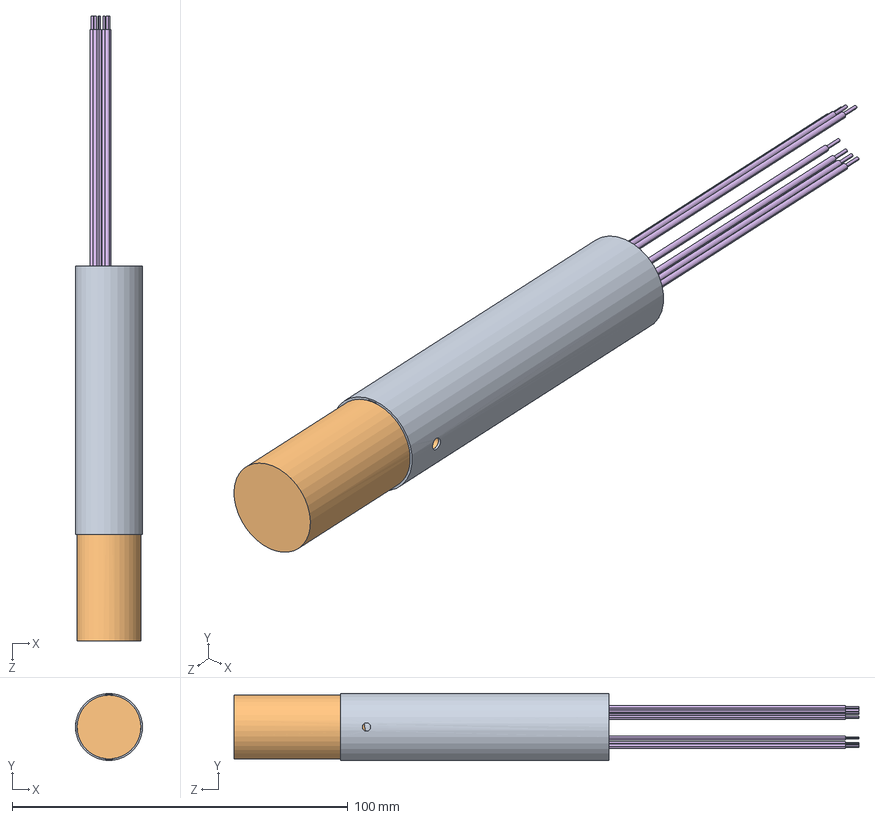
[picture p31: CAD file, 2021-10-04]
Mechanical/Models/SolidWorks/LetItGo.SLDASM
20.0 x 20.0 x 186.2 mm
MotorMount
96095A150_Titanium Threaded Rod
GearBoxMount
drawing_16ecp36.stp
drawing_r16.stp
Socket Head Screw x 6
2006N315_302 Stainless Steel Corrosion-Resistant Compression Springs

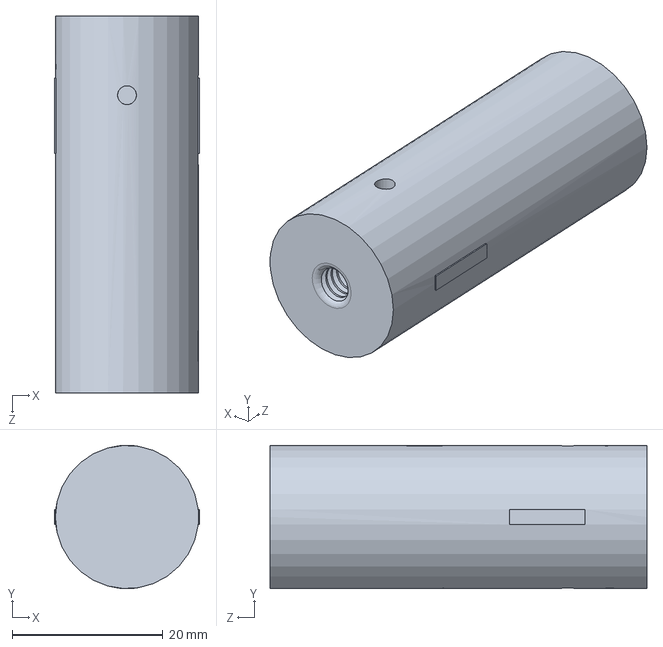
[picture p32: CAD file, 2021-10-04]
Mechanical/Models/SolidWorks/2.SLDPRT
19.2 x 19.0 x 50.0 mm

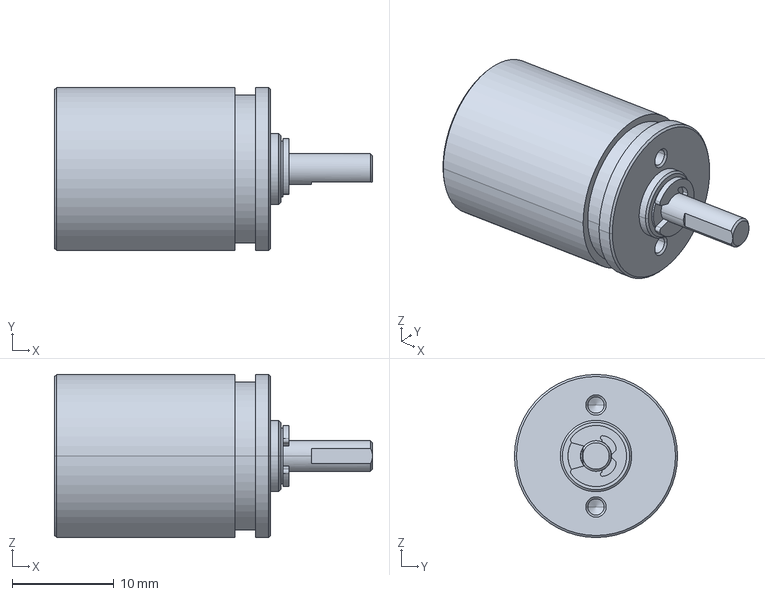
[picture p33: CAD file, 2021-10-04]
Mechanical/Models/SolidWorks/drawing_r16.stp
31.2 x 16.0 x 16.0 mm

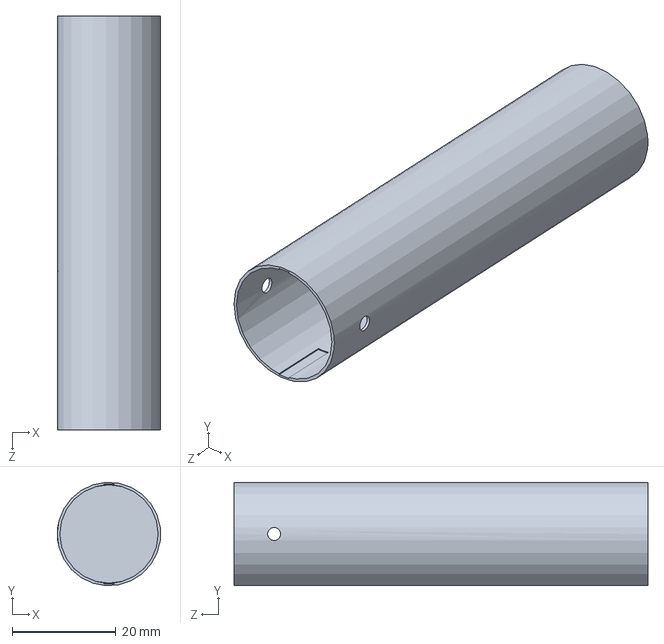
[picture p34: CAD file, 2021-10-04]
Mechanical/Models/SolidWorks/1.SLDPRT
20.0 x 20.0 x 80.0 mm

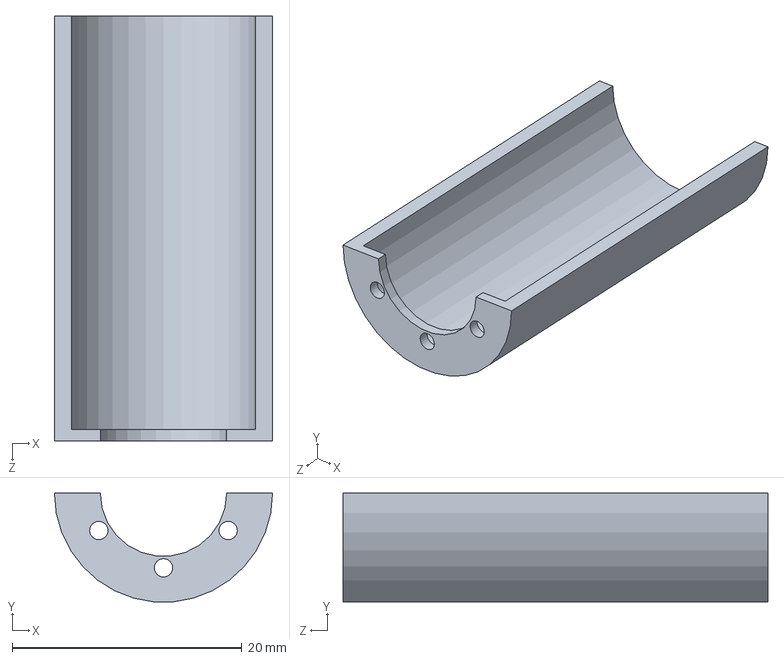
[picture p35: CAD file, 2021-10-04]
Mechanical/Models/SolidWorks/MotorMount.SLDPRT
19.0 x 9.46 x 37.0 mm

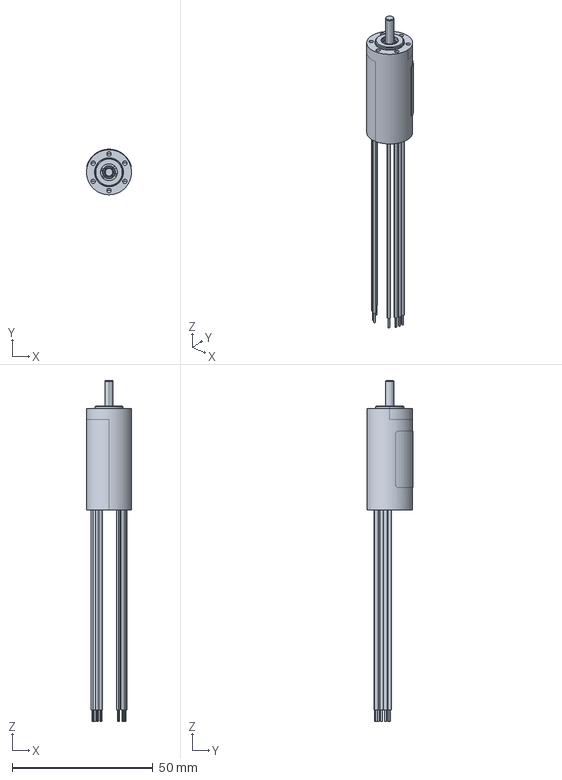
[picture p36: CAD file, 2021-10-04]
Mechanical/Models/SolidWorks/drawing_16ecp36.stp
16.0 x 16.2 x 121.0 mm

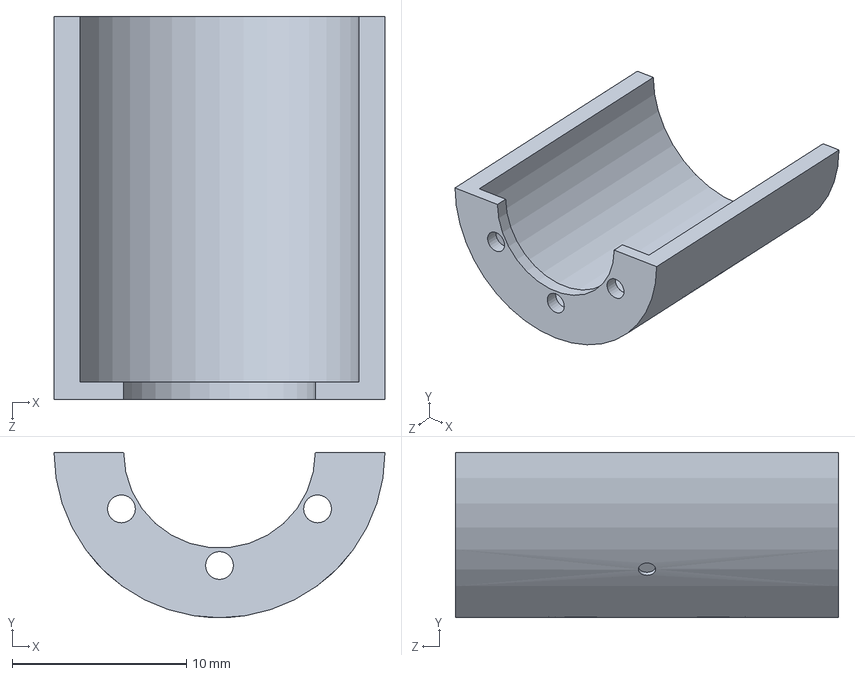
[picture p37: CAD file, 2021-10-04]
Mechanical/Models/SolidWorks/GearBoxMount.SLDPRT
19.0 x 9.50 x 22.0 mm

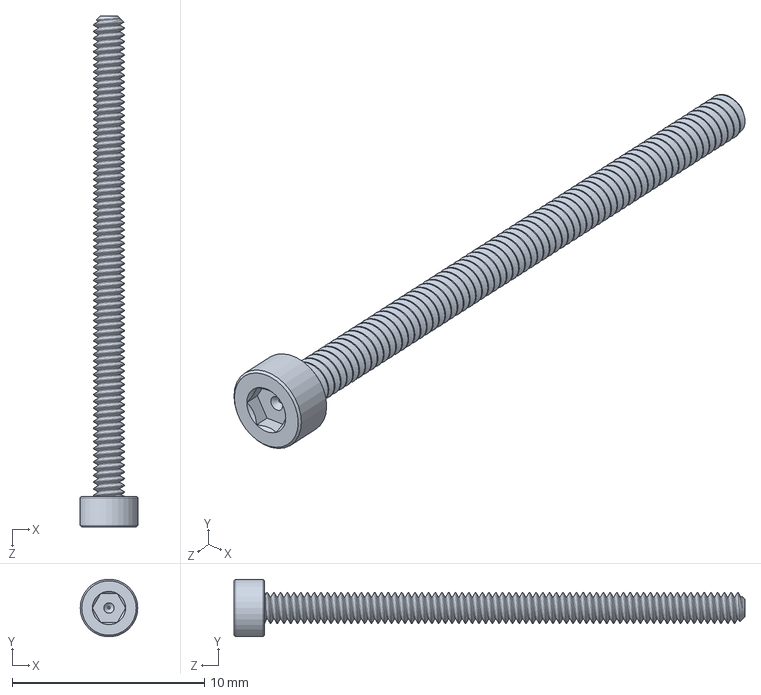
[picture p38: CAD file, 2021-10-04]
Mechanical/Models/SolidWorks/Socket Head Screw.SLDPRT
3.00 x 2.98 x 26.6 mm

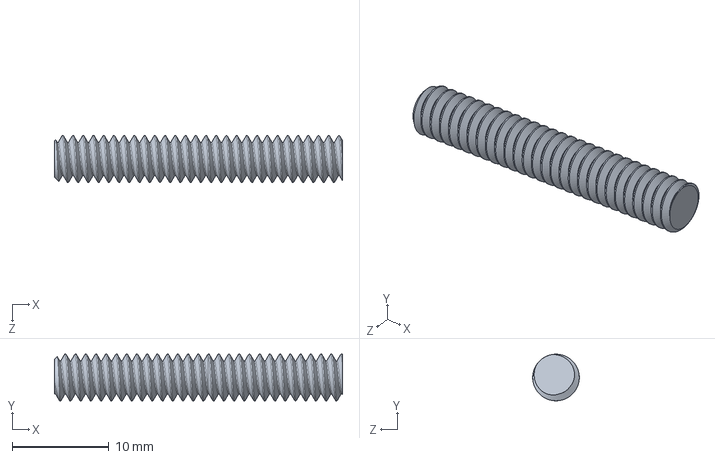
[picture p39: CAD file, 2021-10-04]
Mechanical/Models/SolidWorks/96095A150_Titanium Threaded Rod.SLDPRT
29.8 x 4.83 x 4.83 mm

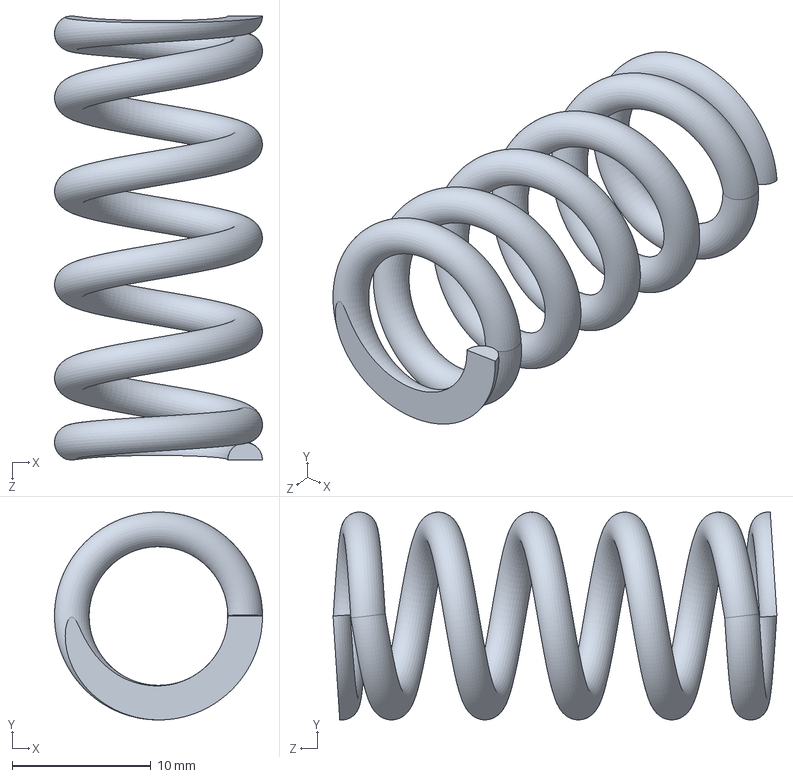
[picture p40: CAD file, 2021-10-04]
Mechanical/Models/SolidWorks/2006N315_302 Stainless Steel Corrosion-Resistant Compression Springs.SLDPRT
15.0 x 15.0 x 32.0 mm

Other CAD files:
Mechanical/Drawings/SolidWorks/1.SLDDRW
Mechanical/Drawings/SolidWorks/2 (1).SLDDRW
Mechanical/Drawings/SolidWorks/96095A150_Titanium Threaded Rod (3).SLDDRW
Mechanical/Drawings/SolidWorks/GearBoxMount (4).SLDDRW
Mechanical/Drawings/SolidWorks/MotorMount.SLDDRW
Mechanical/Drawings/SolidWorks/Socket Head Screw (1).SLDDRW
Mechanical/Drawings/SolidWorks/drawing_16ecp36.SLDDRW
Mechanical/Drawings/SolidWorks/drawing_r16 (1).SLDDRW
Mechanical/Models/SolidWorks/drawing_16ecp36.SLDPRT
Mechanical/Models/SolidWorks/drawing_r16.SLDPRT

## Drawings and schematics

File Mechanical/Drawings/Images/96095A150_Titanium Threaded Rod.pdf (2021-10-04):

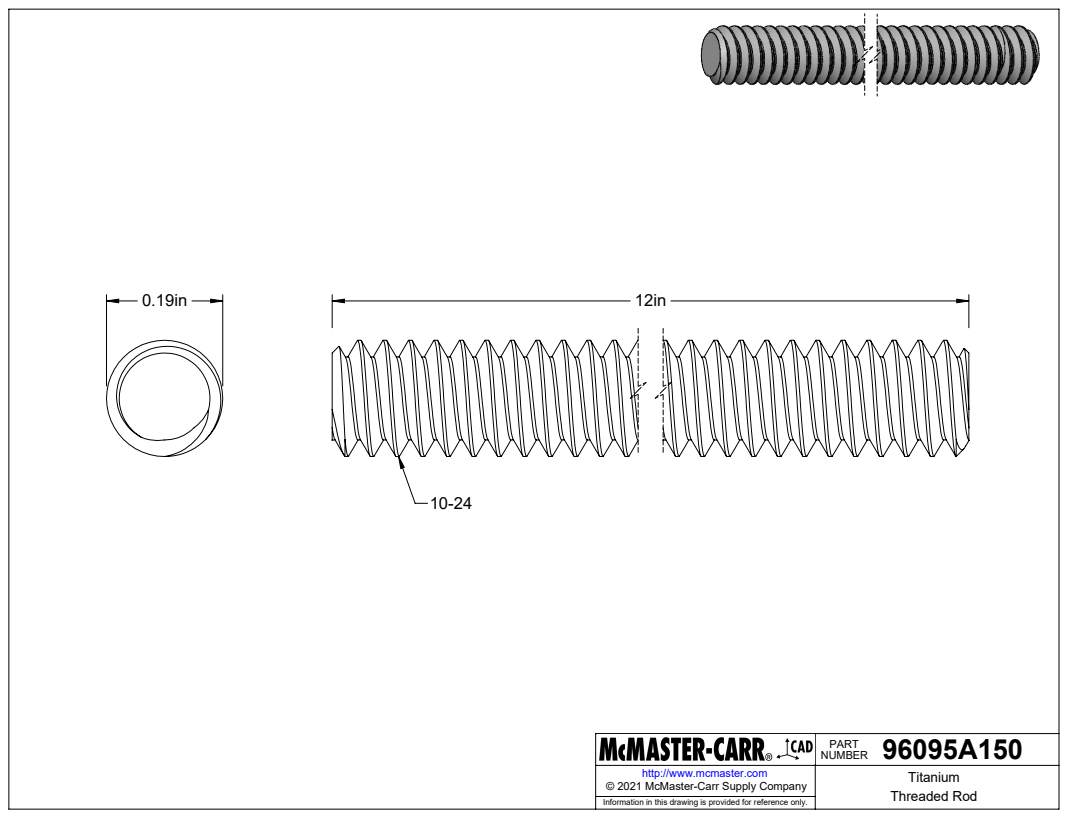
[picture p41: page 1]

96095A150 PART NUMBER

http://www.mcmaster.com | Titanium Threaded Rod © 2021 McMaster-Carr Supply Company

Information in this drawing is provided for reference only.

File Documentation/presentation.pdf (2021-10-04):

# All Screwed Up!

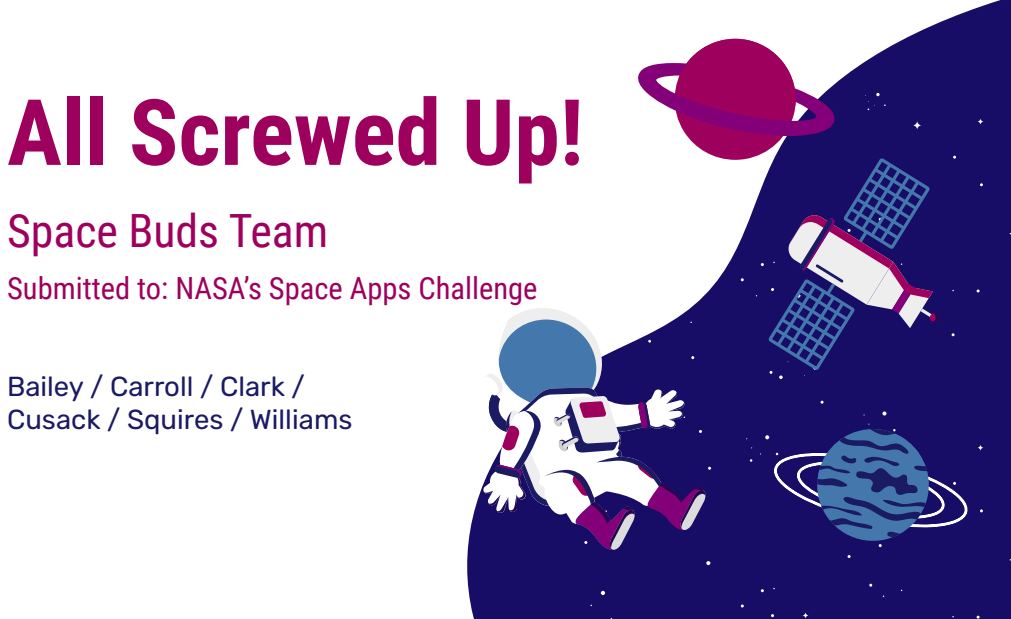
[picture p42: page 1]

Space Buds Team

Submitted to: NASA’s Space Apps Challenge

Bailey / Carroll / Clark /
Cusack / Squires / Williams

# Challenge: Let It Go (Without a Bang)

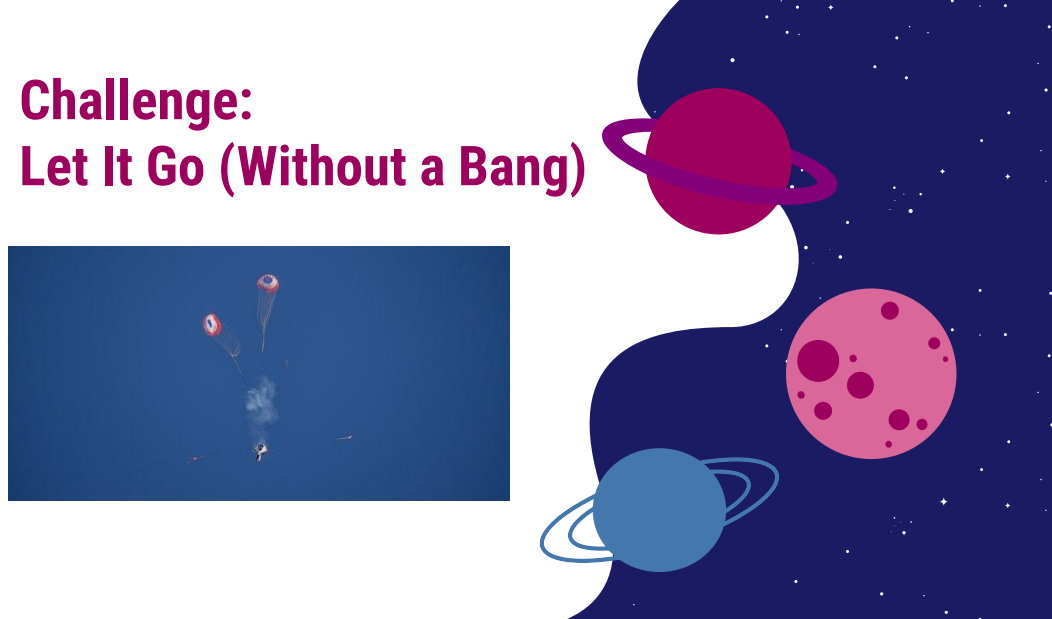
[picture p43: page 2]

# Mechanical Demo

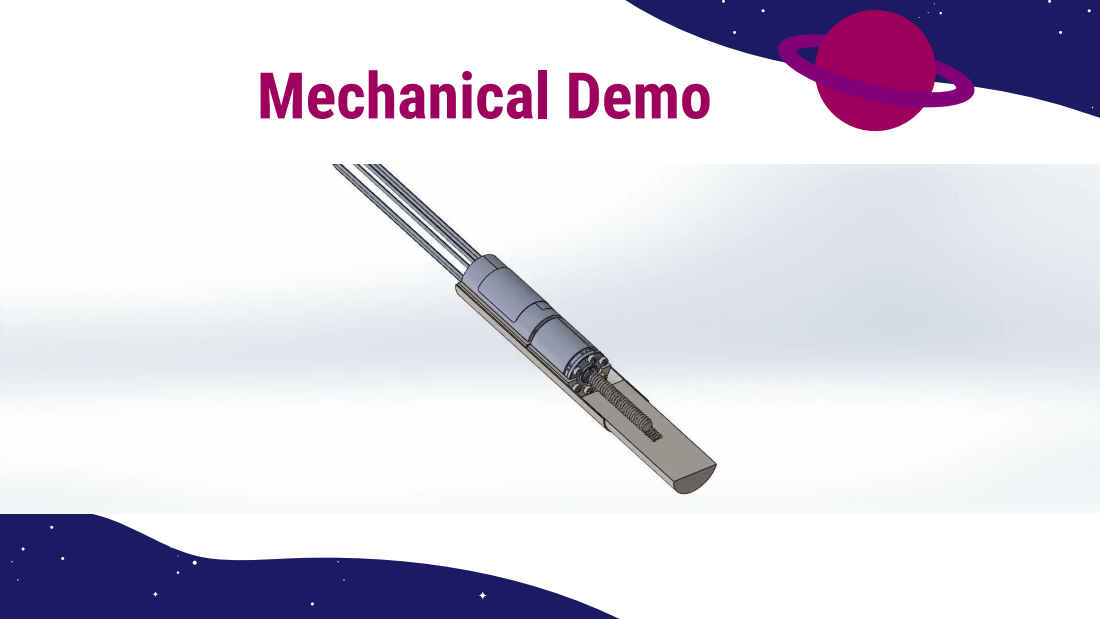
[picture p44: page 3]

# Electrical Design

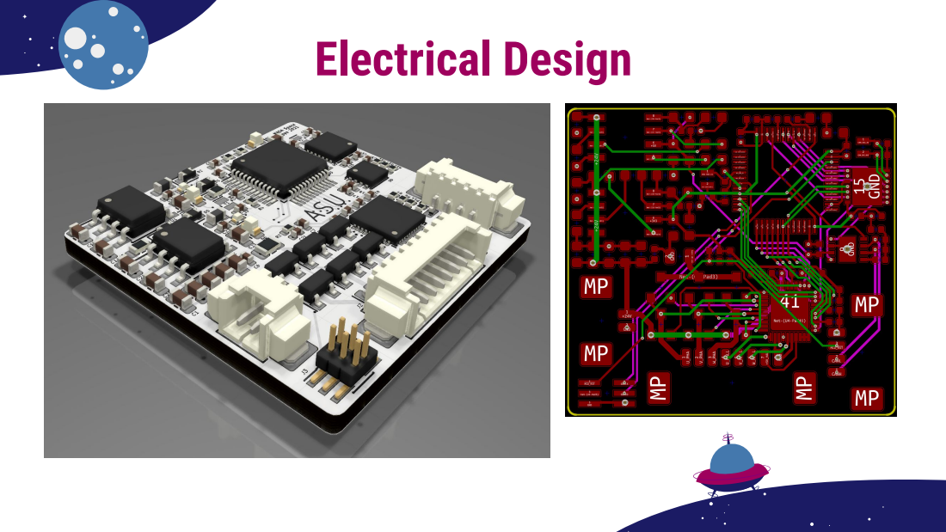
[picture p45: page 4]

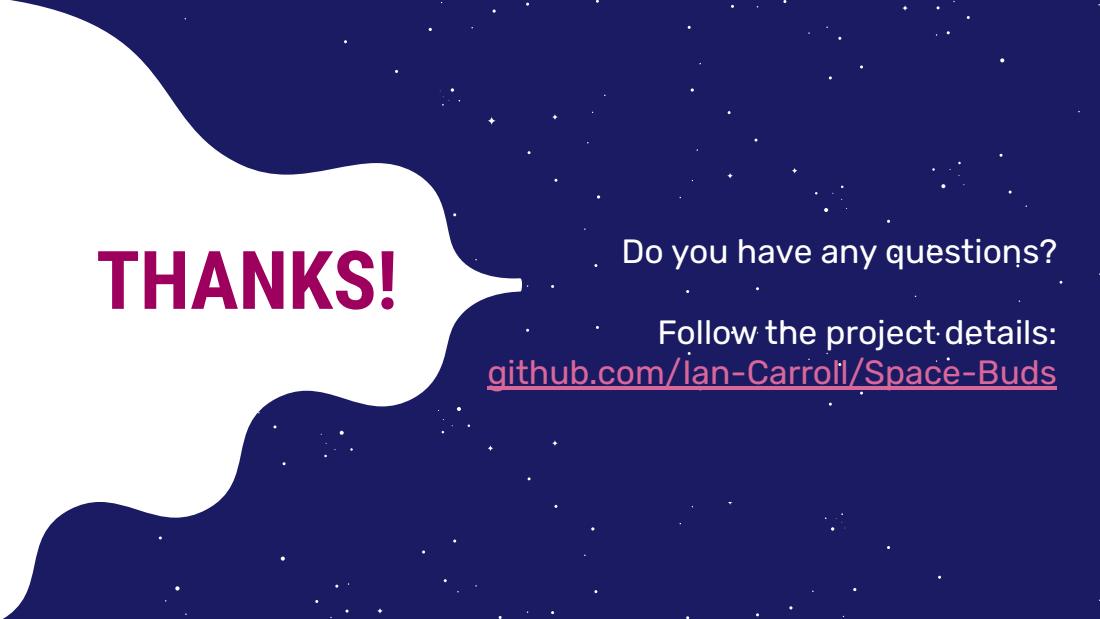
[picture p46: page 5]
CREDITS:; THANKS!; Do you have any questions?

Follow the project details:

github.com/Ian-Carroll/Space-Buds

This presentation template was created by
Slidesgo, (https://slidesgo.com/) including icons by Flaticon, (https://www.flaticon.com/)
infographics & images by Freepik (https://www.freepik.com/)

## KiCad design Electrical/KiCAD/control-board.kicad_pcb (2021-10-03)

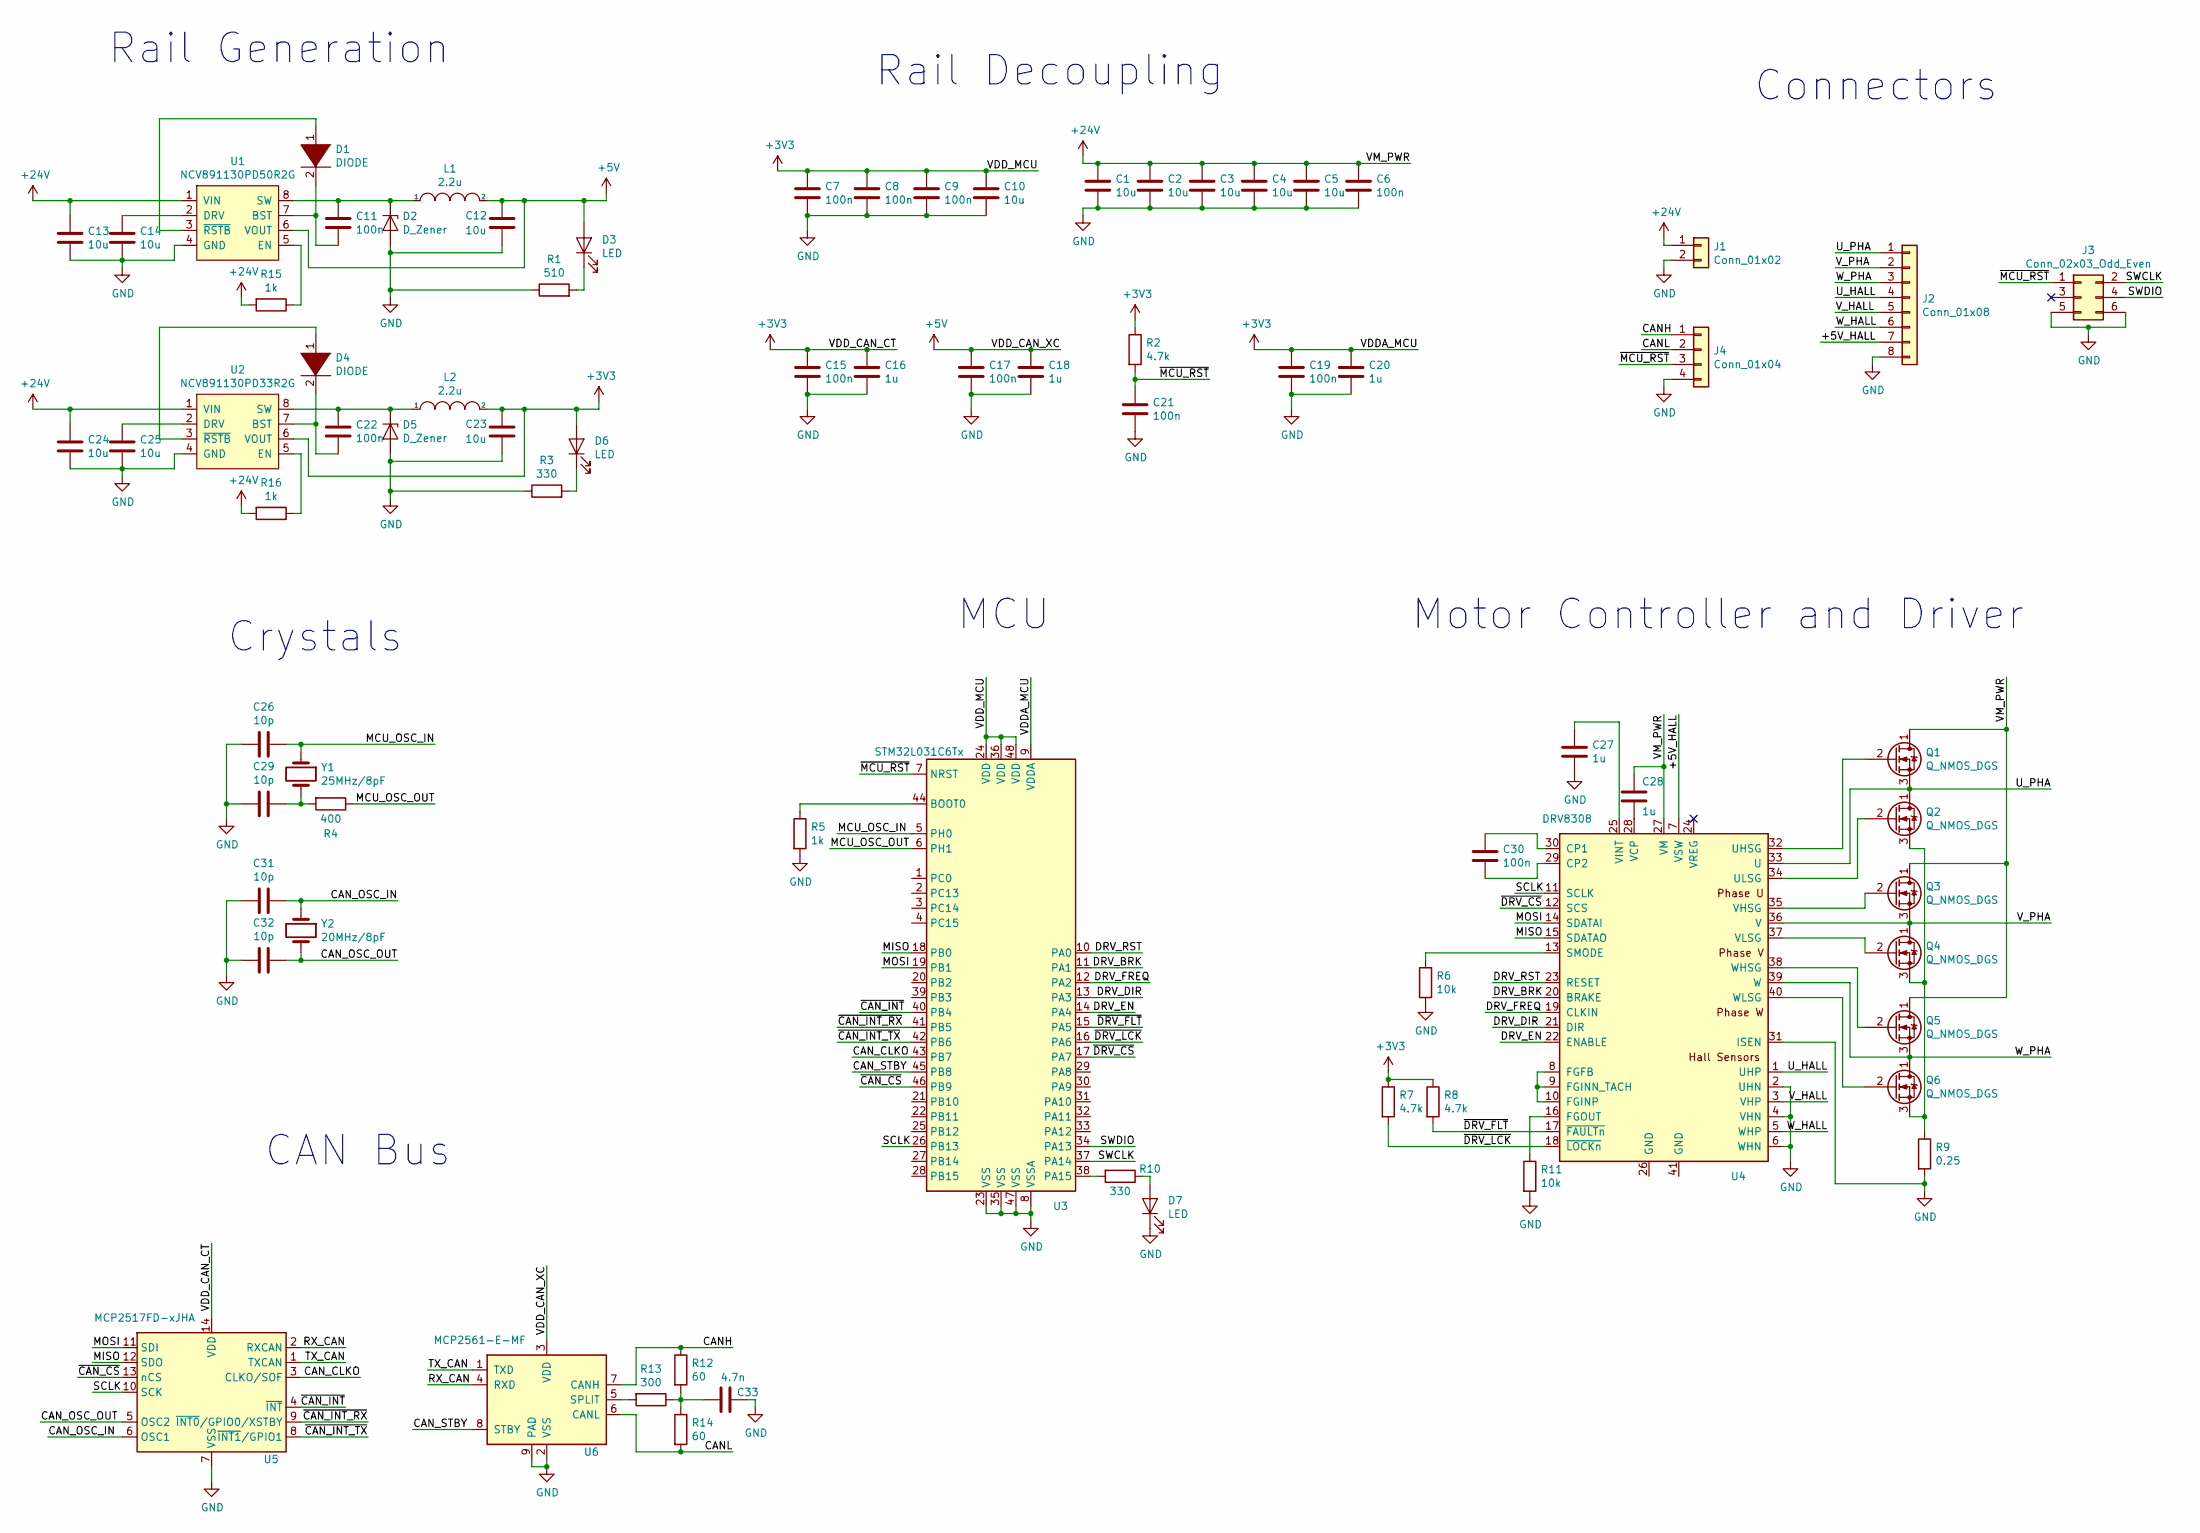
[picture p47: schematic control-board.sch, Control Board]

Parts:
C1, C2, C3, C4, C5, C10, C12, C13, C14, C23, C24, C25: 10u; C_0603_1608Metric
C6, C7, C8, C9, C11, C15, C17, C19, C21, C22, C30: 100n; C_0402_1005Metric
C16, C18, C20, C27, C28: 1u; C_0402_1005Metric
C26, C29, C31, C32: 10p; C_0402_1005Metric
C33: 4.7n; C_0402_1005Metric
D1, D4: DIODE; D_0603_1608Metric
D2, D5: D_Zener; D_0603_1608Metric
D3, D6, D7: LED; LED_0603_1608Metric
J1: Conn_01x02; Molex_PicoBlade_53261-0271_1x02-1MP_P1.25mm_Horizontal
J2: Conn_01x08; Molex_PicoBlade_53261-0871_1x08-1MP_P1.25mm_Horizontal
J3: Conn_02x03_Odd_Even; PinHeader_2x03_P1.00mm_Vertical_SMD
J4: Conn_01x04; Molex_PicoBlade_53261-0471_1x04-1MP_P1.25mm_Horizontal
L1, L2: 2.2u; L_0603_1608Metric
Q1, Q2, Q3, Q4, Q5, Q6: Q_NMOS_DGS; SOT-23
R1: 510; LED_0402_1005Metric
R2, R7, R8: 4.7k; R_0402_1005Metric
R3: 330; LED_0402_1005Metric
R4: 400; R_0402_1005Metric
R5: 1k; R_0402_1005Metric
R6, R11: 10k; R_0402_1005Metric
R9: 0.25; R_0805_2012Metric
R10: 330; R_0402_1005Metric
R12, R14: 60; R_0402_1005Metric
R13: 300; R_0402_1005Metric
R15, R16: 1k; R_0603_1608Metric
U1: NCV891130PD50R2G; SOIC-8_3.9x4.9mm_P1.27mm
U2: NCV891130PD33R2G; SOIC-8_3.9x4.9mm_P1.27mm
U3: STM32L031C6Tx; LQFP-48_7x7mm_P0.5mm
U4: DRV8308; QFN-40-1EP_5x5mm_P0.4mm_EP3.6x3.6mm
U5: MCP2517FD-xJHA; DFN-14-1EP_4x4mm_P0.5mm_EP2.86x3.6mm
U6: MCP2561-E-MF; DFN-8-1EP_3x3mm_P0.65mm_EP1.55x2.4mm
Y1: 25MHz/8pF; Crystal_SMD_MicroCrystal_CM9V-T1A-2Pin_1.6x1.0mm
Y2: 20MHz/8pF; Crystal_SMD_MicroCrystal_CM9V-T1A-2Pin_1.6x1.0mm

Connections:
+3V3: C7.1, C8.1, C9.1, C10.1, C15.1, C16.1, C19.1, C20.1, C23.2, D6.2 (A), L2.2, R2.1, R7.1, R8.1, U2.6 (VOUT), U3.9 (VDDA), U3.24 (VDD), U3.36 (VDD), U3.48 (VDD), U5.14 (VDD)
+5V: C12.2, C17.1, C18.1, D3.2 (A), L1.2, U1.6 (VOUT), U6.3 (VDD)
+24V: C1.1, C2.1, C3.1, C4.1, C5.1, C6.1, C13.1, C24.1, C28.1, J1.1, Q1.1 (D), Q3.1 (D), Q5.1 (D), R15.2, R16.2, U1.1 (VIN), U2.1 (VIN), U4.27 (VM)
/+5V_HALL: J2.7, U4.7 (VSW)
/CANH: J4.1, R12.1, U6.7 (CANH)
/CANL: J4.2, R14.2, U6.6 (CANL)
/CAN_CLKO: U3.43 (PB7), U5.3 (CLKO/SOF)
/CAN_OSC_IN: C31.1, U5.6 (OSC1), Y2.1
/CAN_OSC_OUT: C32.1, U5.5 (OSC2), Y2.2
/CAN_STBY: U3.45 (PB8), U6.8 (STBY)
/DRV_BRK: U3.11 (PA1), U4.20 (BRAKE)
/DRV_DIR: U3.13 (PA3), U4.21 (DIR)
/DRV_EN: U3.14 (PA4), U4.22 (ENABLE)
/DRV_FREQ: U3.12 (PA2), U4.19 (CLKIN)
/DRV_RST: U3.10 (PA0), U4.23 (RESET)
/MCU_OSC_IN: C26.1, U3.5 (PH0), Y1.1
/MCU_OSC_OUT: R4.1, U3.6 (PH1)
/MISO: U3.18 (PB0), U4.15 (SDATAO), U5.12 (SDO)
/MOSI: U3.19 (PB1), U4.14 (SDATAI), U5.11 (SDI)
/RX_CAN: U5.2 (RXCAN), U6.4 (RXD)
/SCLK: U3.26 (PB13), U4.11 (SCLK), U5.10 (SCK)
/SWCLK: J3.2, U3.37 (PA14)
/SWDIO: J3.4, U3.34 (PA13)
/TX_CAN: U5.1 (TXCAN), U6.1 (TXD)
/U_HALL: J2.4, U4.1 (UHP)
/U_PHA: J2.1, Q1.3 (S), Q2.1 (D), U4.33 (U)
/V_HALL: J2.5, U4.3 (VHP)
/V_PHA: J2.2, Q3.3 (S), Q4.1 (D), U4.36 (V)
/W_HALL: J2.6, U4.5 (WHP)
/W_PHA: J2.3, Q5.3 (S), Q6.1 (D), U4.39 (W)
/~CAN_CS: U3.46 (PB9), U5.13 (nCS)
/~CAN_INT: U3.40 (PB4), U5.4 (~INT)
/~CAN_INT_RX: U3.41 (PB5), U5.9 (~INT0~/GPIO0/XSTBY)
/~CAN_INT_TX: U3.42 (PB6), U5.8 (~INT1~/GPIO1)
/~DRV_CS: U3.17 (PA7), U4.12 (SCS)
/~DRV_FLT: R8.2, U3.15 (PA5), U4.17 (~FAULTn)
/~DRV_LCK: R7.2, U3.16 (PA6), U4.18 (~LOCKn)
/~MCU_RST: C21.1, J3.1, J4.3, R2.2, U3.7 (NRST)
GND: C1.2, C2.2, C3.2, C4.2, C5.2, C6.2, C7.2, C8.2, C9.2, C10.2, C12.1, C13.2, C14.2, C15.2, C16.2, C17.2, C18.2, C19.2, C20.2, C21.2, C23.1, C24.2, C25.2, C26.2, C27.2, C29.2, C31.2, C32.2, C33.1, D2.2 (A), D5.2 (A), D7.1 (K), J1.2, J2.8, J3.5, J3.6, J4.4, R1.1, R3.1, R5.2, R6.1, R9.2, R11.2, U1.4 (GND), U2.4 (GND), U3.8 (VSSA), U3.23 (VSS), U3.35 (VSS), U3.47 (VSS), U4.2 (UHN), U4.4 (VHN), U4.6 (WHN), U4.31 (ISEN), U5.7 (VSS), U5.15 (VSS), U6.2 (VSS), U6.9 (PAD)
unnamed: C11.1, D2.1 (K), L1.1, U1.8 (SW)
unnamed: C11.2, D1.2 (A), U1.7 (BST)
unnamed: C14.1, U1.2 (DRV)
unnamed: C22.1, D5.1 (K), L2.1, U2.8 (SW)
unnamed: C22.2, D4.2 (A), U2.7 (BST)
unnamed: C25.1, U2.2 (DRV)
unnamed: C27.1, U4.25 (VINT)
unnamed: C28.2, U4.28 (VCP)
unnamed: C29.1, R4.2, Y1.2
unnamed: C30.1, U4.30 (CP1)
unnamed: C30.2, U4.29 (CP2)
unnamed: C33.2, R12.2, R13.1, R14.1
unnamed: D1.1 (K), U1.3 (~RSTB)
unnamed: D3.1 (K), R1.2
unnamed: D4.1 (K), U2.3 (~RSTB)
unnamed: D6.1 (K), R3.2
unnamed: D7.2 (A), R10.1
unnamed: Q1.2 (G), U4.32 (UHSG)
unnamed: Q2.2 (G), U4.34 (ULSG)
unnamed: Q2.3 (S), Q4.3 (S), Q6.3 (S), R9.1
unnamed: Q3.2 (G), U4.35 (VHSG)
unnamed: Q4.2 (G), U4.37 (VLSG)
unnamed: Q5.2 (G), U4.38 (WHSG)
unnamed: Q6.2 (G), U4.40 (WLSG)
unnamed: R5.1, U3.44 (BOOT0)
unnamed: R6.2, U4.13 (SMODE)
unnamed: R10.2, U3.38 (PA15)
unnamed: R11.1, U4.16 (FGOUT)
unnamed: R13.2, U6.5 (SPLIT)
unnamed: R15.1, U1.5 (EN)
unnamed: R16.1, U2.5 (EN)
unnamed: U4.8 (FGFB), U4.9 (FGINN_TACH), U4.10 (FGINP)

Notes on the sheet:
Rail Generation
Rail Decoupling
Crystals
CAN Bus
MCU
Motor Controller and Driver
Connectors

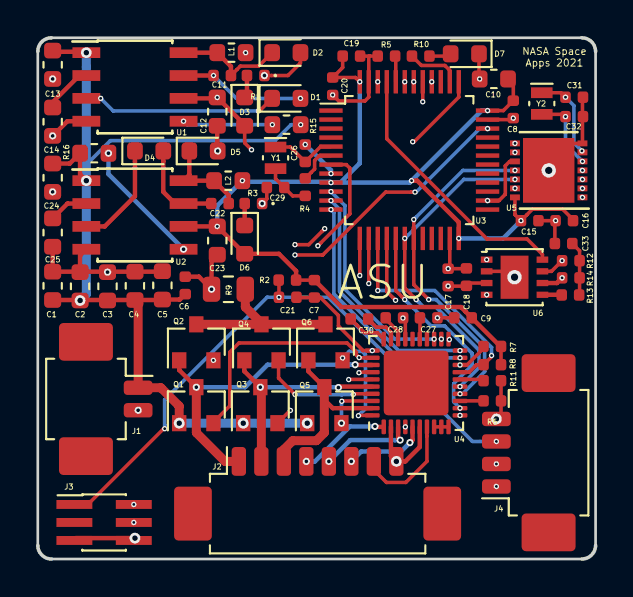
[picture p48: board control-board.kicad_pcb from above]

Board: 4 copper layers, 31.0 x 29.0 mm, 76 parts (0 on the bottom side), 71 nets.

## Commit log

2021-10-03 Add PCB CAD files.
    [control-board.kicad_pcb, control-board.sch]
2021-10-03 Add PCB renders.
2021-10-03 Add PCB layout and schematic.
2021-10-04 Rename electrical directories.
    [control-board.kicad_pcb, control-board.sch]
2021-10-04 Add mechanical drawings.
    [1.SLDDRW, 2 (1).SLDDRW, 96095A150_Titanium Threaded Rod (3).SLDDRW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]
2021-10-04 Add mechanical models.
    [1.SLDPRT, 2.SLDPRT, 2006N315_302 Stainless Steel Corrosion-Resistant Compression Springs.SLDPRT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]
2021-10-04 Rename SolidWorks directories.
    [1.SLDDRW, 1.SLDPRT, 2 (1).SLDDRW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]
